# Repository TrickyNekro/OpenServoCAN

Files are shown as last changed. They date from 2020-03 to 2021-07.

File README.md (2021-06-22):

# OpenServoCAN
by El. Provatos

<b>!!! Currently two versions of the Hardware exist, development is going to continue on version 2 !!!</b><br>
<b>!!! Note: There is a design problem ( mechanical fitting ) with the power board, wait for update !!!</b>

An alternative to the boring control boards inside standard size hobby servos!

As it is, the project is far from completion! I have the first boards already, but I do not
have the materials to populate them. I will most probably start a gofundme campaign for these
first stages of the project. So bear with me, this will be an on-going process!

It was a very long time I wanted to make a project like this
Most, for the more expensive ones, hobby servos offer no feed back.
You send them a signal and hope they will reach the targeted position.
This might be good enough for uses in the RC world, but not good enough 
at all for those building robots or anything of a kind that needs feedback.

And thus this project was born! Although I am aware that another OpenServo Project
exists, I wanted to put my own touch into the matter and I tried to do quite a few 
things better, at least compared to the first version (I have not reviewed the second).

- Hardware V1 Capabilities

1) Added CAN-Bus! Yes, that´s a good thing! It might complicate some things especially for beginners
but that´s on what most "unobtainium" servos work in the market. I have not yet decided the 
communications protocol, but I am leaning towards CANopen, suggestions are open!

2) Can support either a potentiometer or an encoder (quadrature or not) for positional control

3) Can operate from 5V - 15V safe zone, but most probably will not have a problem with a 4S LiPo.
Current limiting will be done by software so, if you want to break the DC motor inside or not is
totally up to you!

4) Beefed up MOSFETs with individual MOSFET drivers, just to be able to push that switching 
frequency to the right spot without worrying too much!

- Hardware V2 Capabilities ( added on top of the previous! )

1) Modular! Yes, Modular! There is a Power Board, a CPU / MCU board and a Sensor / Encoder Board.
All are connected on the same bus, through some nice 0,5mm pitch - 30 pin Amphenol connectors. 
That also means of course that everything can change, and the version in connected to the function
specific board and not the whole system. Bored of the microcontroller? Change the MCU board, need
higher voltage? Change the power board? Need more capabilities? If physically allowed, add more
boards! Etc. etc. etc.. 

2) This version uses a magnetic encoder from AMS! Have not tested it yet, but given that it works
well without much interference from the motor, it should be able to give both precision, speed and
universality to the adaptation of the design. And do not forget... bored of the encoder board? Need
something more simple? Design and change it with a potentiometer board! Easy Peasy!!! 

3) One of the main limitation of the previous version was the input voltage. 15V max? How boring! 
This version was aimed to work with 24V and pushing it to 30V should be no problem! Unfortunately
the 100% duty cycle capability is gone as well, but the more efficient all N-Channel MOSFET bridge
should be able to make up the difference! Even if it does not, this was the one big step in being
able to bridge the design to a higher operating voltage, given the much constrained space.

4) There is a digital power meter from Texas Instruments on-board, should offload the processor 
quite a bit! And has also some quite interesting interrupt capabilites that should come in handy.

5) MCU board now has, EEPROM, battery (or better Super-Cap) backed RTC, a temperature sensor and
an RGB LED! How can one live without RGB these days. In all seriousness though, the RTC and EEPROM
should be a good compination for logging data / events and or even be used to wake the device up,
or even be able to develop small scripts for the device to run autonomously. But that´s only a dream
for now, still capability is there!

6) Reverse polarity protection is still here! But I also added some small extras! Some "TVS - like"
suppressors here, some more distributed capacitance there. It should be less noisy and more stable.
Only time will tell as more and more code and testing is being done!

<b> Important 2/11/2020 Update! </b>
I have officially ended the fundraiser for this Project. True to my promise I would like to thank:
Juri Ludwig, Anonymous (from eevblog ;-) ), Vagelis Logaras and Andreas Efthymiadis for their contributions.
Their money have funded a couple mouser orders, the PCBs and some test servos. Which for me is more than
enough that anyone would do for an open project with an open completion date! I can only promise that I
will continue to deliver as much as real life allows me. Thank you! Let your names be immortalized here!

# Donations!

<b>No project on the internet would be great without donations! And Crypto is the future! </b>

In Elon Musk We Trust Dogecoin (DOGE) : DQTDoTPzMencAXoiDVByQjifk2DryYTUPZ <br>
For the old timers Bitcoin (BTC)      : bc1qxqq8dz8md20nyglan9hmk88s894f8h0ywm0fq3 <br>
For the Russian hackers Ethereum(ETH) : 0xAA05e9abD960005df318Ab82aE35A8c47e0096AB <br>

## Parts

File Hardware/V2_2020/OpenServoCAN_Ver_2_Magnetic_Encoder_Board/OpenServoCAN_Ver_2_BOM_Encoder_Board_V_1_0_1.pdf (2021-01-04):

OpenServoCAN_Ver_2_BOM_Encoder_Board_V_1_0_1

Part | Value | Device | Package | Description | Shopping Link | Datasheet
C301 | 100n | GCM155R71H104KE02J | 0402_C | Standard 0402 Capacitor with European Symbol | GCM155R71H104KE02J (https://www.mouser.de/ProductDetail/Murata-Electronics/GCM155R71H104KE02J/?qs=hNud%2FORuBR1wlwGPFWBVDg%3D%3D) | GCM155R71H104KE02J (https://www.mouser.de/datasheet/2/281/murata_03122018_GCM_Series-1310150.pdf)
C302 | 10u | GRM155R60J106ME15D | 0402_C | Standard 0402 Capacitor with European Symbol | GRM155R60J106ME15D (https://www.mouser.de/ProductDetail/Murata-Electronics/GRM155R60J106ME15D/?qs=I53XXhTNm8s65u6%252BR3mHqw%3D%3D) | GRM155R60J106ME15D (https://www.mouser.de/datasheet/2/281/murata_03052018_GRM_Series_1-1310166.pdf)
C303 | 10u | GRM155R60J106ME15D | 0402_C | Standard 0402 Capacitor with European Symbol | GRM155R60J106ME15D (https://www.mouser.de/ProductDetail/Murata-Electronics/GRM155R60J106ME15D/?qs=I53XXhTNm8s65u6%252BR3mHqw%3D%3D) | GRM155R60J106ME15D (https://www.mouser.de/datasheet/2/281/murata_03052018_GRM_Series_1-1310166.pdf)
C304 | 100n | GCM155R71H104KE02J | 0402_C | Standard 0402 Capacitor with European Symbol | GCM155R71H104KE02J (https://www.mouser.de/ProductDetail/Murata-Electronics/GCM155R71H104KE02J/?qs=hNud%2FORuBR1wlwGPFWBVDg%3D%3D) | GCM155R71H104KE02J (https://www.mouser.de/datasheet/2/281/murata_03122018_GCM_Series-1310150.pdf)
C305 | 100n | GCM155R71H104KE02J | 0402_C | Standard 0402 Capacitor with European Symbol | GCM155R71H104KE02J (https://www.mouser.de/ProductDetail/Murata-Electronics/GCM155R71H104KE02J/?qs=hNud%2FORuBR1wlwGPFWBVDg%3D%3D) | GCM155R71H104KE02J (https://www.mouser.de/datasheet/2/281/murata_03122018_GCM_Series-1310150.pdf)
C306 | 100n | GCM155R71H104KE02J | 0402_C | Standard 0402 Capacitor with European Symbol | GCM155R71H104KE02J (https://www.mouser.de/ProductDetail/Murata-Electronics/GCM155R71H104KE02J/?qs=hNud%2FORuBR1wlwGPFWBVDg%3D%3D) | GCM155R71H104KE02J (https://www.mouser.de/datasheet/2/281/murata_03122018_GCM_Series-1310150.pdf)
C307 | 100n | GCM155R71H104KE02J | 0402_C | Standard 0402 Capacitor with European Symbol | GCM155R71H104KE02J (https://www.mouser.de/ProductDetail/Murata-Electronics/GCM155R71H104KE02J/?qs=hNud%2FORuBR1wlwGPFWBVDg%3D%3D) | GCM155R71H104KE02J (https://www.mouser.de/datasheet/2/281/murata_03122018_GCM_Series-1310150.pdf)
C308 | 10u | GRM155R60J106ME15D | 0402_C | Standard 0402 Capacitor with European Symbol | GRM155R60J106ME15D (https://www.mouser.de/ProductDetail/Murata-Electronics/GRM155R60J106ME15D/?qs=I53XXhTNm8s65u6%252BR3mHqw%3D%3D) | GRM155R60J106ME15D (https://www.mouser.de/datasheet/2/281/murata_03052018_GRM_Series_1-1310166.pdf)
C309 | 100n | GCM155R71H104KE02J | 0402_C | Standard 0402 Capacitor with European Symbol | GCM155R71H104KE02J (https://www.mouser.de/ProductDetail/Murata-Electronics/GCM155R71H104KE02J/?qs=hNud%2FORuBR1wlwGPFWBVDg%3D%3D) | GCM155R71H104KE02J (https://www.mouser.de/datasheet/2/281/murata_03122018_GCM_Series-1310150.pdf)
C310 | DMS3R3224R | DMS3R3224R | DMS_3R3_S_CAP | DMS 3R3 0.2 - 0.3 F @ 3V3 6.8X1.8 Coin Super Cap | DMS3R3224R (https://www.reichelt.com/smd-superkondensator-0-22-f-3-3-v-1000-h-ko-dms3r3224r-p244465.html) | DMS3R3224R (https://cdn-reichelt.de/documents/datenblatt/B300/DMS.pdf)
C311 | 100n | GCM155R71H104KE02J | 0402_C | Standard 0402 Capacitor with European Symbol | GCM155R71H104KE02J (https://www.mouser.de/ProductDetail/Murata-Electronics/GCM155R71H104KE02J/?qs=hNud%2FORuBR1wlwGPFWBVDg%3D%3D) | GCM155R71H104KE02J (https://www.mouser.de/datasheet/2/281/murata_03122018_GCM_Series-1310150.pdf)
C312 | 100n | GCM155R71H104KE02J | 0402_C | Standard 0402 Capacitor with European Symbol | GCM155R71H104KE02J (https://www.mouser.de/ProductDetail/Murata-Electronics/GCM155R71H104KE02J/?qs=hNud%2FORuBR1wlwGPFWBVDg%3D%3D) | GCM155R71H104KE02J (https://www.mouser.de/datasheet/2/281/murata_03122018_GCM_Series-1310150.pdf)
IC301 | AS5048A-HTSP-500 | AS5048A-HTSP-500 | TSSOP-14 | 14-bit Angular Position Sensor | AS5048A-HTSP-500 (https://www.mouser.de/ProductDetail/ams/AS5048A-HTSP-500/?qs=YVUHYZFLFLutJ5C0elRlwQ%3D%3D) | AS5048A-HTSP-500 (https://www.mouser.de/datasheet/2/588/AS5048_DS000298_4-00-1100510.pdf)
IC302 | SN74LV1T126DCKRG4 | SN74LV1T126DCKRG4 | SC-70-5 | Single Buffer Gate with 3-State Output | SN74LV1T126DCKRG4 (https://www.mouser.de/ProductDetail/Texas-Instruments/SN74LV1T126DCKRG4/?qs=qSfuJ%252Bfl%2Fd7XMpUR4BtXdA%3D%3D) | SN74LV1T126DCKRG4 (https://www.ti.com/lit/ds/symlink/sn74lv1t126.pdf)
IC303 | SN74LV1T126DCKRG4 | SN74LV1T126DCKRG4 | SC-70-5 | Single Buffer Gate with 3-State Output | SN74LV1T126DCKRG4 (https://www.mouser.de/ProductDetail/Texas-Instruments/SN74LV1T126DCKRG4/?qs=qSfuJ%252Bfl%2Fd7XMpUR4BtXdA%3D%3D) | SN74LV1T126DCKRG4 (https://www.ti.com/lit/ds/symlink/sn74lv1t126.pdf)
IC304 | SN74LV1T126DCKRG4 | SN74LV1T126DCKRG4 | SC-70-5 | Single Buffer Gate with 3-State Output | SN74LV1T126DCKRG4 (https://www.mouser.de/ProductDetail/Texas-Instruments/SN74LV1T126DCKRG4/?qs=qSfuJ%252Bfl%2Fd7XMpUR4BtXdA%3D%3D) | SN74LV1T126DCKRG4 (https://www.ti.com/lit/ds/symlink/sn74lv1t126.pdf)
IC305 | SN74LV1T126DCKRG4 | SN74LV1T126DCKRG4 | SC-70-5 | Single Buffer Gate with 3-State Output | SN74LV1T126DCKRG4 (https://www.mouser.de/ProductDetail/Texas-Instruments/SN74LV1T126DCKRG4/?qs=qSfuJ%252Bfl%2Fd7XMpUR4BtXdA%3D%3D) | SN74LV1T126DCKRG4 (https://www.ti.com/lit/ds/symlink/sn74lv1t126.pdf)
IC306 | TPS79933QDDCRQ1 | TPS79933QDDCRQ1 | SOT-23-5 | LDO 3.3V Voltage Regulators 200mA Output | TPS79933QDDCRQ1 (https://www.mouser.de/ProductDetail/Texas-Instruments/TPS79933QDDCRQ1/?qs=O3wcJz4o8IfzUKU6paImvQ%3D%3D) | TPS79933QDDCRQ1 (https://www.ti.com/lit/ds/symlink/tps799-q1.pdf)
J301 | 10132798-032100LF | 10132798-032100LF | 10132798-032100LF | Amphenol BergStak ® 0.5mm Mezzanine Connector | 10132798-032100LF (https://www.mouser.de/ProductDetail/Amphenol-FCI/10132798-032100LF/) | 10132798-032100LF (https://www.amphenol-icc.com/media/wysiwyg/files/documentation/datasheet/boardwiretoboard/bwb_bergstak_05mm_mezzanine.pdf)
R301 | 100K | ERJ-2RKF1003X | 0402_R | Standard 0402 Resistor with American Symbol | ERJ-2RKF1003X (https://www.mouser.de/ProductDetail/Panasonic/ERJ-2RKF1003X/?qs=sGAEpiMZZMtlubZbdhIBIHcx2Q2RnT7K1YMPDp9rJM8%3D) | ERJ-2RKF1003X (https://www.mouser.de/datasheet/2/315/AOA0000C304-1149620.pdf)
R302 | 100K | ERJ-2RKF1003X | 0402_R | Standard 0402 Resistor with American Symbol | ERJ-2RKF1003X (https://www.mouser.de/ProductDetail/Panasonic/ERJ-2RKF1003X/?qs=sGAEpiMZZMtlubZbdhIBIHcx2Q2RnT7K1YMPDp9rJM8%3D) | ERJ-2RKF1003X (https://www.mouser.de/datasheet/2/315/AOA0000C304-1149620.pdf)
R303 | 100K | ERJ-2RKF1003X | 0402_R | Standard 0402 Resistor with American Symbol | ERJ-2RKF1003X (https://www.mouser.de/ProductDetail/Panasonic/ERJ-2RKF1003X/?qs=sGAEpiMZZMtlubZbdhIBIHcx2Q2RnT7K1YMPDp9rJM8%3D) | ERJ-2RKF1003X (https://www.mouser.de/datasheet/2/315/AOA0000C304-1149620.pdf)
R304 | 100K | ERJ-2RKF1003X | 0402_R | Standard 0402 Resistor with American Symbol | ERJ-2RKF1003X (https://www.mouser.de/ProductDetail/Panasonic/ERJ-2RKF1003X/?qs=sGAEpiMZZMtlubZbdhIBIHcx2Q2RnT7K1YMPDp9rJM8%3D) | ERJ-2RKF1003X (https://www.mouser.de/datasheet/2/315/AOA0000C304-1149620.pdf)
R305 | 100K | ERJ-2RKF1003X | 0402_R | Standard 0402 Resistor with American Symbol | ERJ-2RKF1003X (https://www.mouser.de/ProductDetail/Panasonic/ERJ-2RKF1003X/?qs=sGAEpiMZZMtlubZbdhIBIHcx2Q2RnT7K1YMPDp9rJM8%3D) | ERJ-2RKF1003X (https://www.mouser.de/datasheet/2/315/AOA0000C304-1149620.pdf)
R306 | 100K | ERJ-2RKF1003X | 0402_R | Standard 0402 Resistor with American Symbol | ERJ-2RKF1003X (https://www.mouser.de/ProductDetail/Panasonic/ERJ-2RKF1003X/?qs=sGAEpiMZZMtlubZbdhIBIHcx2Q2RnT7K1YMPDp9rJM8%3D) | ERJ-2RKF1003X (https://www.mouser.de/datasheet/2/315/AOA0000C304-1149620.pdf)
R307 | 100K | ERJ-2RKF1003X | 0402_R | Standard 0402 Resistor with American Symbol | ERJ-2RKF1003X (https://www.mouser.de/ProductDetail/Panasonic/ERJ-2RKF1003X/?qs=sGAEpiMZZMtlubZbdhIBIHcx2Q2RnT7K1YMPDp9rJM8%3D) | ERJ-2RKF1003X (https://www.mouser.de/datasheet/2/315/AOA0000C304-1149620.pdf)
R308 | 100K | ERJ-2RKF1003X | 0402_R | Standard 0402 Resistor with American Symbol | ERJ-2RKF1003X (https://www.mouser.de/ProductDetail/Panasonic/ERJ-2RKF1003X/?qs=sGAEpiMZZMtlubZbdhIBIHcx2Q2RnT7K1YMPDp9rJM8%3D) | ERJ-2RKF1003X (https://www.mouser.de/datasheet/2/315/AOA0000C304-1149620.pdf)
R309 | 47 | ERJ-2RKF47R0X | 0402_R | Standard 0402 Resistor with American Symbol | ERJ-2RKF47R0X (https://www.mouser.de/ProductDetail/Panasonic/ERJ-2RKF47R0X/) | ERJ-2RKF47R0X (https://www.mouser.de/datasheet/2/315/AOA0000C304-1149620.pdf)
R310 | 47 | ERJ-2RKF47R0X | 0402_R | Standard 0402 Resistor with American Symbol | ERJ-2RKF47R0X (https://www.mouser.de/ProductDetail/Panasonic/ERJ-2RKF47R0X/) | ERJ-2RKF47R0X (https://www.mouser.de/datasheet/2/315/AOA0000C304-1149620.pdf)
R311 | 47 | ERJ-2RKF47R0X | 0402_R | Standard 0402 Resistor with American Symbol | ERJ-2RKF47R0X (https://www.mouser.de/ProductDetail/Panasonic/ERJ-2RKF47R0X/) | ERJ-2RKF47R0X (https://www.mouser.de/datasheet/2/315/AOA0000C304-1149620.pdf)
R312 | 47 | ERJ-2RKF47R0X | 0402_R | Standard 0402 Resistor with American Symbol | ERJ-2RKF47R0X (https://www.mouser.de/ProductDetail/Panasonic/ERJ-2RKF47R0X/) | ERJ-2RKF47R0X (https://www.mouser.de/datasheet/2/315/AOA0000C304-1149620.pdf)
R313 | 1k | ERJ-2RKF1001X | 0402_R | Standard 0402 Resistor with American Symbol | ERJ-2RKF1001X (https://www.mouser.de/ProductDetail/Panasonic/ERJ-2RKF1001X/) | ERJ-2RKF1001X (https://www.mouser.de/datasheet/2/315/AOA0000C304-1149620.pdf)
R314 | 1k | ERJ-2RKF1001X | 0402_R | Standard 0402 Resistor with American Symbol | ERJ-2RKF1001X (https://www.mouser.de/ProductDetail/Panasonic/ERJ-2RKF1001X/) | ERJ-2RKF1001X (https://www.mouser.de/datasheet/2/315/AOA0000C304-1149620.pdf)
R315 | 470 | ERJ-2RKF4700X | 0402_R | Standard 0402 Resistor with American Symbol | ERJ-2RKF4700X (https://www.mouser.de/ProductDetail/Panasonic/ERJ-2RKF4700X/) | ERJ-2RKF4700X (https://www.mouser.de/datasheet/2/315/AOA0000C304-1149620.pdf)
R316 | 10 | ERJ-2RKF10R0X | 0402_R | Standard 0402 Resistor with American Symbol | ERJ-2RKF10R0X (https://www.mouser.de/ProductDetail/Panasonic/ERJ-2RKF10R0X/) | ERJ-2RKF10R0X (https://www.mouser.de/datasheet/2/315/AOA0000C304-1149620.pdf)
R317 | 10 | ERJ-2RKF10R0X | 0402_R | Standard 0402 Resistor with American Symbol | ERJ-2RKF10R0X (https://www.mouser.de/ProductDetail/Panasonic/ERJ-2RKF10R0X/) | ERJ-2RKF10R0X (https://www.mouser.de/datasheet/2/315/AOA0000C304-1149620.pdf)
R318 | 1k | ERJ-2RKF1001X | 0402_R | Standard 0402 Resistor with American Symbol | ERJ-2RKF1001X (https://www.mouser.de/ProductDetail/Panasonic/ERJ-2RKF1001X/) | ERJ-2RKF1001X (https://www.mouser.de/datasheet/2/315/AOA0000C304-1149620.pdf)
T301 | UMX1NFHATN | UMX1NFHATN | SC-70-6 | Bipolar Transistor Pair ( NPN + NPN ) | UMX1NFHATN (https://www.mouser.de/ProductDetail/ROHM-Semiconductor/UMX1NFHATN/) | UMX1NFHATN (https://www.mouser.de/datasheet/2/348/umx1nfha-e-1872402.pdf)

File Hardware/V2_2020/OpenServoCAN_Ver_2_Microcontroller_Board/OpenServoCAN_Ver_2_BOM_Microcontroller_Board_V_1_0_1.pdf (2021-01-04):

OpenServoCAN_Ver_2_Microcontroller_Board_V_1_0_1

Part | Value | Device | Package | Description | Shopping Link | Datasheet
C201 | 100n | GCM155R71H104KE02J | 0402_C | Standard 0402 Capacitor with European Symbol | GCM155R71H104KE02J (https://www.mouser.de/ProductDetail/Murata-Electronics/GCM155R71H104KE02J/?qs=hNud%2FORuBR1wlwGPFWBVDg%3D%3D) | GCM155R71H104KE02J (https://www.mouser.de/datasheet/2/281/murata_03122018_GCM_Series-1310150.pdf)
C202 | 2u2 | LMK105BJ225KV-F | 0402_C | Standard 0402 Capacitor with European Symbol | LMK105BJ225KV-F (https://www.mouser.de/ProductDetail/Taiyo-Yuden/LMK105BJ225KV-F/) | LMK105BJ225KV-F (https://www.mouser.de/datasheet/2/396/mlcc02_e-1307760.pdf)
C203 | 100n | GCM155R71H104KE02J | 0402_C | Standard 0402 Capacitor with European Symbol | GCM155R71H104KE02J (https://www.mouser.de/ProductDetail/Murata-Electronics/GCM155R71H104KE02J/?qs=hNud%2FORuBR1wlwGPFWBVDg%3D%3D) | GCM155R71H104KE02J (https://www.mouser.de/datasheet/2/281/murata_03122018_GCM_Series-1310150.pdf)
C204 | 100n | GCM155R71H104KE02J | 0402_C | Standard 0402 Capacitor with European Symbol | GCM155R71H104KE02J (https://www.mouser.de/ProductDetail/Murata-Electronics/GCM155R71H104KE02J/?qs=hNud%2FORuBR1wlwGPFWBVDg%3D%3D) | GCM155R71H104KE02J (https://www.mouser.de/datasheet/2/281/murata_03122018_GCM_Series-1310150.pdf)
C205 | 100n | GCM155R71H104KE02J | 0402_C | Standard 0402 Capacitor with European Symbol | GCM155R71H104KE02J (https://www.mouser.de/ProductDetail/Murata-Electronics/GCM155R71H104KE02J/?qs=hNud%2FORuBR1wlwGPFWBVDg%3D%3D) | GCM155R71H104KE02J (https://www.mouser.de/datasheet/2/281/murata_03122018_GCM_Series-1310150.pdf)
C206 | 22p | 04025A220JAT4A | 0402_C | Standard 0402 Capacitor with European Symbol | 04025A220JAT4A (https://www.mouser.de/ProductDetail/AVX/04025A220JAT4A/?qs=i7%252BfZ0iplmWikHQFZS%252BeyA%3D%3D) | 04025A220JAT4A (https://www.mouser.de/datasheet/2/40/C0GNP0_Dielectric-951274.pdf)
C207 | 22p | 04025A220JAT4A | 0402_C | Standard 0402 Capacitor with European Symbol | 04025A220JAT4A (https://www.mouser.de/ProductDetail/AVX/04025A220JAT4A/?qs=i7%252BfZ0iplmWikHQFZS%252BeyA%3D%3D) | 04025A220JAT4A (https://www.mouser.de/datasheet/2/40/C0GNP0_Dielectric-951274.pdf)
C208 | 100n | GCM155R71H104KE02J | 0402_C | Standard 0402 Capacitor with European Symbol | GCM155R71H104KE02J (https://www.mouser.de/ProductDetail/Murata-Electronics/GCM155R71H104KE02J/?qs=hNud%2FORuBR1wlwGPFWBVDg%3D%3D) | GCM155R71H104KE02J (https://www.mouser.de/datasheet/2/281/murata_03122018_GCM_Series-1310150.pdf)
C209 | 100n | GCM155R71H104KE02J | 0402_C | Standard 0402 Capacitor with European Symbol | GCM155R71H104KE02J (https://www.mouser.de/ProductDetail/Murata-Electronics/GCM155R71H104KE02J/?qs=hNud%2FORuBR1wlwGPFWBVDg%3D%3D) | GCM155R71H104KE02J (https://www.mouser.de/datasheet/2/281/murata_03122018_GCM_Series-1310150.pdf)
C210 | 100n | GCM155R71H104KE02J | 0402_C | Standard 0402 Capacitor with European Symbol | GCM155R71H104KE02J (https://www.mouser.de/ProductDetail/Murata-Electronics/GCM155R71H104KE02J/?qs=hNud%2FORuBR1wlwGPFWBVDg%3D%3D) | GCM155R71H104KE02J (https://www.mouser.de/datasheet/2/281/murata_03122018_GCM_Series-1310150.pdf)
IC201 | PIC18F26K83-I/ML | PIC18F26K83-I/ML | QFN-28 | PIC18(L)F25/26K83 | PIC18F26K83-I/ML (https://www.mouser.de/ProductDetail/Microchip-Technology/PIC18F26K83-I-ML/) | PIC18F26K83-I/ML (https://www.mouser.de/datasheet/2/268/40001943A-1222654.pdf)
IC202 | MCP9808T-E/MC | MCP9808T-E/MC | DFN_2X3_MICROCHIP | MCP9808 | MCP9808T-E/MC (https://www.mouser.de/ProductDetail/Microchip-Technology/MCP9808T-E-MC/) | MCP9808T-E/MC (https://www.mouser.de/datasheet/2/268/25095A-15487.pdf)
IC203 | MCP7940NT-I/MNY | MCP7940NT-I/MNY | DFN_2X3_MICROCHIP | MCP7940N | MCP7940NT-I/MNY (https://www.mouser.de/ProductDetail/Microchip-Technology/MCP7940NT-I-MNY/) | MCP7940NT-I/MNY (https://www.mouser.de/datasheet/2/268/25010A-71550.pdf)
IC204 | 24LC64T-E/MNY | 24LC64T-E/MNY | DFN_2X3_MICROCHIP | 24LCxx Type EEPROM | 24LC64T-E/MNY (https://www.mouser.de/ProductDetail/Microchip-Technology/24LC64T-E-MNY/) | 24LC64T-E/MNY (https://www.mouser.de/datasheet/2/268/21189T-264996.pdf)
J201 | 53047-0510 | PIC-ICSP-MICRO | PICOBLADE-5 | Microchip PIC ICSP based on a 5 PIN Molex PICO-Blade | 53047-0510 (https://www.mouser.de/ProductDetail/Molex/53047-0510/) | 53047-0510 (https://www.mouser.de/datasheet/2/276/0530470510_PCB_HEADERS-171009.pdf)
J202 | 10132798-032100LF | 10132798-032100LF | 10132798-032100LF | Amphenol BergStak ® 0.5mm Mezzanine Connector | 10132798-032100LF (https://www.mouser.de/ProductDetail/Amphenol-FCI/10132798-032100LF/) | 10132798-032100LF (https://www.amphenol-icc.com/media/wysiwyg/files/documentation/datasheet/boardwiretoboard/bwb_bergstak_05mm_mezzanine.pdf)
J203 | 10132797-035100LF | 10132797-035100LF | 10132797-035100LF | Amphenol BergStak ® 0.5mm Mezzanine Connector | 10132797-035100LF (https://www.mouser.de/ProductDetail/Amphenol-FCI/10132797-035100LF/) | 10132797-035100LF (https://www.amphenol-icc.com/media/wysiwyg/files/documentation/datasheet/boardwiretoboard/bwb_bergstak_05mm_mezzanine.pdf)
LED201 | IN-S126TASRGB | IN-S126TASRGB | 1206_RGB_LED | Side View RGB LED from Lite-On | IN-S126TASRGB (https://www.mouser.de/ProductDetail/Inolux/IN-S126TASRGB/) | IN-S126TASRGB (https://www.mouser.de/datasheet/2/180/IN_S126TASRGB_V1_1-1488266.pdf)
Q201 | LFXTAL009678 | LFXTAL009678 | LFXTAL009678 | LFXTAL009678 | LFXTAL009678 (https://www.mouser.de/Search/Refine?Keyword=LFXTAL009678) | LFXTAL009678 (https://www.mouser.de/datasheet/2/741/LFXTAL009678Cutt-952301.pdf)
R201 | 4k7 | ERJ-2RKF4701X | 0402_R | Standard 0402 Resistor with American Symbol | ERJ-2RKF4701X (https://www.mouser.de/ProductDetail/Panasonic/ERJ-2RKF4701X/) | ERJ-2RKF4701X (https://www.mouser.de/datasheet/2/315/AOA0000C304-1149620.pdf)
R202 | 470 | ERJ-2RKF4700X | 0402_R | Standard 0402 Resistor with American Symbol | ERJ-2RKF4700X (https://www.mouser.de/ProductDetail/Panasonic/ERJ-2RKF4700X/) | ERJ-2RKF4700X (https://www.mouser.de/datasheet/2/315/AOA0000C304-1149620.pdf)
R203 | 220 | ERJ-2RKF2200X | 0402_R | Standard 0402 Resistor with American Symbol | ERJ-2RKF2200X (https://www.mouser.de/ProductDetail/Panasonic/ERJ-2RKF2200X/) | ERJ-2RKF2200X (https://www.mouser.de/datasheet/2/315/AOA0000C304-1149620.pdf)
R204 | 220 | ERJ-2RKF2200X | 0402_R | Standard 0402 Resistor with American Symbol | ERJ-2RKF2200X (https://www.mouser.de/ProductDetail/Panasonic/ERJ-2RKF2200X/) | ERJ-2RKF2200X (https://www.mouser.de/datasheet/2/315/AOA0000C304-1149620.pdf)
R205 | 220 | ERJ-2RKF2200X | 0402_R | Standard 0402 Resistor with American Symbol | ERJ-2RKF2200X (https://www.mouser.de/ProductDetail/Panasonic/ERJ-2RKF2200X/) | ERJ-2RKF2200X (https://www.mouser.de/datasheet/2/315/AOA0000C304-1149620.pdf)
R206 | 4k7 | ERJ-2RKF4701X | 0402_R | Standard 0402 Resistor with American Symbol | ERJ-2RKF4701X (https://www.mouser.de/ProductDetail/Panasonic/ERJ-2RKF4701X/) | ERJ-2RKF4701X (https://www.mouser.de/datasheet/2/315/AOA0000C304-1149620.pdf)
R207 | 4k7 | ERJ-2RKF4701X | 0402_R | Standard 0402 Resistor with American Symbol | ERJ-2RKF4701X (https://www.mouser.de/ProductDetail/Panasonic/ERJ-2RKF4701X/) | ERJ-2RKF4701X (https://www.mouser.de/datasheet/2/315/AOA0000C304-1149620.pdf)
R208 | 4k7 | ERJ-2RKF4701X | 0402_R | Standard 0402 Resistor with American Symbol | ERJ-2RKF4701X (https://www.mouser.de/ProductDetail/Panasonic/ERJ-2RKF4701X/) | ERJ-2RKF4701X (https://www.mouser.de/datasheet/2/315/AOA0000C304-1149620.pdf)
R209 | 4k7 | ERJ-2RKF4701X | 0402_R | Standard 0402 Resistor with American Symbol | ERJ-2RKF4701X (https://www.mouser.de/ProductDetail/Panasonic/ERJ-2RKF4701X/) | ERJ-2RKF4701X (https://www.mouser.de/datasheet/2/315/AOA0000C304-1149620.pdf)
R210 | 470 | ERJ-2RKF4700X | 0402_R | Standard 0402 Resistor with American Symbol | ERJ-2RKF4700X (https://www.mouser.de/ProductDetail/Panasonic/ERJ-2RKF4700X/) | ERJ-2RKF4700X (https://www.mouser.de/datasheet/2/315/AOA0000C304-1149620.pdf)
R211 | 470 | ERJ-2RKF4700X | 0402_R | Standard 0402 Resistor with American Symbol | ERJ-2RKF4700X (https://www.mouser.de/ProductDetail/Panasonic/ERJ-2RKF4700X/) | ERJ-2RKF4700X (https://www.mouser.de/datasheet/2/315/AOA0000C304-1149620.pdf)
R212 | 47 | ERJ-2RKF47R0X | 0402_R | Standard 0402 Resistor with American Symbol | ERJ-2RKF47R0X (https://www.mouser.de/ProductDetail/Panasonic/ERJ-2RKF47R0X/) | ERJ-2RKF47R0X (https://www.mouser.de/datasheet/2/315/AOA0000C304-1149620.pdf)
R213 | 47 | ERJ-2RKF47R0X | 0402_R | Standard 0402 Resistor with American Symbol | ERJ-2RKF47R0X (https://www.mouser.de/ProductDetail/Panasonic/ERJ-2RKF47R0X/) | ERJ-2RKF47R0X (https://www.mouser.de/datasheet/2/315/AOA0000C304-1149620.pdf)
R214 | 47 | ERJ-2RKF47R0X | 0402_R | Standard 0402 Resistor with American Symbol | ERJ-2RKF47R0X (https://www.mouser.de/ProductDetail/Panasonic/ERJ-2RKF47R0X/) | ERJ-2RKF47R0X (https://www.mouser.de/datasheet/2/315/AOA0000C304-1149620.pdf)

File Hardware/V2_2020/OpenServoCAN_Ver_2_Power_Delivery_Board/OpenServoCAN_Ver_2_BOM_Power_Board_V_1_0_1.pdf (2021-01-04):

OpenServoCAN_Ver_2_BOM_Power_Board_V_1_0_1

Part | Value | Device | Package | Description | Shopping Link | Datasheet
C101 | 220n | CL10A224KB8NNNC | 0603_C | Standard 0603 Capacitor with European Symbol | CL10A224KB8NNNC (https://www.mouser.de/ProductDetail/Samsung-Electro-Mechanics/CL10A224KB8NNNC/?qs=uwxL4vQweFONfCk4qeShcQ%3D%3D) | CL10A224KB8NNNC (https://www.mouser.de/datasheet/2/585/MLCC-1837944.pdf)
C102 | 220n | CL10A224KB8NNNC | 0603_C | Standard 0603 Capacitor with European Symbol | CL10A224KB8NNNC (https://www.mouser.de/ProductDetail/Samsung-Electro-Mechanics/CL10A224KB8NNNC/?qs=uwxL4vQweFONfCk4qeShcQ%3D%3D) | CL10A224KB8NNNC (https://www.mouser.de/datasheet/2/585/MLCC-1837944.pdf)
C103 | 10u | GRM155R60J106ME15D | 0402_C | Standard 0402 Capacitor with European Symbol | GRM155R60J106ME15D (https://www.mouser.de/ProductDetail/Murata-Electronics/GRM155R60J106ME15D/?qs=I53XXhTNm8s65u6%252BR3mHqw%3D%3D) | GRM155R60J106ME15D (https://www.mouser.de/datasheet/2/281/murata_03052018_GRM_Series_1-1310166.pdf)
C104 | 10u | GRM155R60J106ME15D | 0402_C | Standard 0402 Capacitor with European Symbol | GRM155R60J106ME15D (https://www.mouser.de/ProductDetail/Murata-Electronics/GRM155R60J106ME15D/?qs=I53XXhTNm8s65u6%252BR3mHqw%3D%3D) | GRM155R60J106ME15D (https://www.mouser.de/datasheet/2/281/murata_03052018_GRM_Series_1-1310166.pdf)
C105 | 100n | GCM155R71H104KE02J | 0402_C | Standard 0402 Capacitor with European Symbol | GCM155R71H104KE02J (https://www.mouser.de/ProductDetail/Murata-Electronics/GCM155R71H104KE02J/?qs=hNud%2FORuBR1wlwGPFWBVDg%3D%3D) | GCM155R71H104KE02J (https://www.mouser.de/datasheet/2/281/murata_03122018_GCM_Series-1310150.pdf)
C106 | 100n | GCM155R71H104KE02J | 0402_C | Standard 0402 Capacitor with European Symbol | GCM155R71H104KE02J (https://www.mouser.de/ProductDetail/Murata-Electronics/GCM155R71H104KE02J/?qs=hNud%2FORuBR1wlwGPFWBVDg%3D%3D) | GCM155R71H104KE02J (https://www.mouser.de/datasheet/2/281/murata_03122018_GCM_Series-1310150.pdf)
C107 | 100n | GCM155R71H104KE02J | 0402_C | Standard 0402 Capacitor with European Symbol | GCM155R71H104KE02J (https://www.mouser.de/ProductDetail/Murata-Electronics/GCM155R71H104KE02J/?qs=hNud%2FORuBR1wlwGPFWBVDg%3D%3D) | GCM155R71H104KE02J (https://www.mouser.de/datasheet/2/281/murata_03122018_GCM_Series-1310150.pdf)
C108 | 10u | GRM155R60J106ME15D | 0402_C | Standard 0402 Capacitor with European Symbol | GRM155R60J106ME15D (https://www.mouser.de/ProductDetail/Murata-Electronics/GRM155R60J106ME15D/?qs=I53XXhTNm8s65u6%252BR3mHqw%3D%3D) | GRM155R60J106ME15D (https://www.mouser.de/datasheet/2/281/murata_03052018_GRM_Series_1-1310166.pdf)
C109 | 10u | GRM155R60J106ME15D | 0402_C | Standard 0402 Capacitor with European Symbol | GRM155R60J106ME15D (https://www.mouser.de/ProductDetail/Murata-Electronics/GRM155R60J106ME15D/?qs=I53XXhTNm8s65u6%252BR3mHqw%3D%3D) | GRM155R60J106ME15D (https://www.mouser.de/datasheet/2/281/murata_03052018_GRM_Series_1-1310166.pdf)
C110 | 1u | CL10A105KB8NNNC | 0603_C | Standard 0603 Capacitor with European Symbol | CL10A105KB8NNNC (https://www.mouser.de/ProductDetail/Samsung-Electro-Mechanics/CL10A105KB8NNNC/?qs=ktYoCbbtCSJz4pFCLWXd5g%3D%3D) | CL10A105KB8NNNC (https://www.mouser.de/datasheet/2/585/MLCC-1837944.pdf)
C111 | 1u | CL10A105KB8NNNC | 0603_C | Standard 0603 Capacitor with European Symbol | CL10A105KB8NNNC (https://www.mouser.de/ProductDetail/Samsung-Electro-Mechanics/CL10A105KB8NNNC/?qs=ktYoCbbtCSJz4pFCLWXd5g%3D%3D) | CL10A105KB8NNNC (https://www.mouser.de/datasheet/2/585/MLCC-1837944.pdf)
C112 | 1u | CL10A105KB8NNNC | 0603_C | Standard 0603 Capacitor with European Symbol | CL10A105KB8NNNC (https://www.mouser.de/ProductDetail/Samsung-Electro-Mechanics/CL10A105KB8NNNC/?qs=ktYoCbbtCSJz4pFCLWXd5g%3D%3D) | CL10A105KB8NNNC (https://www.mouser.de/datasheet/2/585/MLCC-1837944.pdf)
C113 | 1u | CL10A105KB8NNNC | 0603_C | Standard 0603 Capacitor with European Symbol | CL10A105KB8NNNC (https://www.mouser.de/ProductDetail/Samsung-Electro-Mechanics/CL10A105KB8NNNC/?qs=ktYoCbbtCSJz4pFCLWXd5g%3D%3D) | CL10A105KB8NNNC (https://www.mouser.de/datasheet/2/585/MLCC-1837944.pdf)
C114 | 1u | CL10A105KB8NNNC | 0603_C | Standard 0603 Capacitor with European Symbol | CL10A105KB8NNNC (https://www.mouser.de/ProductDetail/Samsung-Electro-Mechanics/CL10A105KB8NNNC/?qs=ktYoCbbtCSJz4pFCLWXd5g%3D%3D) | CL10A105KB8NNNC (https://www.mouser.de/datasheet/2/585/MLCC-1837944.pdf)
C115 | 1u | CL10A105KB8NNNC | 0603_C | Standard 0603 Capacitor with European Symbol | CL10A105KB8NNNC (https://www.mouser.de/ProductDetail/Samsung-Electro-Mechanics/CL10A105KB8NNNC/?qs=ktYoCbbtCSJz4pFCLWXd5g%3D%3D) | CL10A105KB8NNNC (https://www.mouser.de/datasheet/2/585/MLCC-1837944.pdf)
C116 | 1u | CL10A105KB8NNNC | 0603_C | Standard 0603 Capacitor with European Symbol | CL10A105KB8NNNC (https://www.mouser.de/ProductDetail/Samsung-Electro-Mechanics/CL10A105KB8NNNC/?qs=ktYoCbbtCSJz4pFCLWXd5g%3D%3D) | CL10A105KB8NNNC (https://www.mouser.de/datasheet/2/585/MLCC-1837944.pdf)
C117 | 10n | GCM155R71H103KA55D | 0402_C | Standard 0402 Capacitor with European Symbol | GCM155R71H103KA55D (https://www.mouser.de/ProductDetail/Murata-Electronics/GCM155R71H103KA55D/?qs=aEuGZpxfbxUFaK62TPaKIA%3D%3D) | GCM155R71H103KA55D (https://www.mouser.de/datasheet/2/281/murata_03122018_GCM_Series-1310150.pdf)
C118 | 470p | CC1206JRNPO0BN471 | 1206_C | Standard 1206 Capacitor with European Symbol | CC1206JRNPO0BN471 (https://www.mouser.de/ProductDetail/Yageo/CC1206JRNPO0BN471/?qs=AgBp2OyFlx8rV3mvW5uGXA%3D%3D) | CC1206JRNPO0BN471 (https://www.mouser.de/datasheet/2/447/UPY_NP0X7R_MV_100_to_630V_21-1947934.pdf)
C119 | 47p | CC1206JRNPO0BN470 | 1206_C | Standard 1206 Capacitor with European Symbol | CC1206JRNPO0BN470 (https://www.mouser.de/ProductDetail/Yageo/CC1206JRNPO0BN470/) | CC1206JRNPO0BN470 (https://www.mouser.de/datasheet/2/447/UPY_NP0X7R_MV_100_to_630V_21-1947934.pdf)
C120 | 47p | CC1206JRNPO0BN470 | 1206_C | Standard 1206 Capacitor with European Symbol | CC1206JRNPO0BN470 (https://www.mouser.de/ProductDetail/Yageo/CC1206JRNPO0BN470/) | CC1206JRNPO0BN470 (https://www.mouser.de/datasheet/2/447/UPY_NP0X7R_MV_100_to_630V_21-1947934.pdf)
D101 | DDZ12CSF-7 | DDZ12CSF-7 | SOD-323 | Zener Diodes 500mW 12.05V Zener 0.07uA 11.20 | DDZ12CSF-7 (https://www.mouser.de/ProductDetail/Diodes-Incorporated/DDZ12CSF-7/) | DDZ12CSF-7 (https://www.mouser.de/datasheet/2/115/ds31987-65362.pdf)
D102 | PMEG4010ESBYL | PMEG4010ESBYL | DSN1006-2 | 40 V, 1 A low VF MEGA Schottky | PMEG4010ESBYL (https://www.mouser.de/ProductDetail/Nexperia/PMEG4010ESBYL/?qs=bel5lzaZNxTQEUPrzEQoCw%3D%3D) | PMEG4010ESBYL (https://www.mouser.de/datasheet/2/916/PMEG4010ESB-1320302.pdf)
D103 | TVS2701DRBR | TVS2701DRBR | VSON-8-DRB0008A | TVSxx01 Series of Texas Instruments Fast-Clamp TVS | TVS2701DRBR (https://www.mouser.de/ProductDetail/Texas-Instruments/TVS2701DRBR/) | TVS2701DRBR (https://www.ti.com/lit/ds/symlink/tvs2701.pdf)
D104 | TVS2700DRVR | TVS2700DRVR | WSON-6 | TVSxx00 Series of Texas Instruments Fast-Clamp TVS | TVS2700DRVR (https://www.mouser.de/ProductDetail/Texas-Instruments/TVS2700DRVR/) | TVS2700DRVR (https://www.ti.com/lit/ds/symlink/tvs2700.pdf)
IC101 | MCP14700-E/MF | MCP14700-E/MF | DFN_8_3X3X09_MF | Dual Input Synchronous MOSFET Driver | MCP14700-E/MF (https://www.mouser.de/ProductDetail/Microchip-Technology/MCP14700-E-MF/?qs=X8nz4ozed5gysS6OQjCf4w%3D%3D) | MCP14700-E/MF (https://www.mouser.de/datasheet/2/268/22201a-53003.pdf)
IC102 | MCP14700-E/MF | MCP14700-E/MF | DFN_8_3X3X09_MF | Dual Input Synchronous MOSFET Driver | MCP14700-E/MF (https://www.mouser.de/ProductDetail/Microchip-Technology/MCP14700-E-MF/?qs=X8nz4ozed5gysS6OQjCf4w%3D%3D) | MCP14700-E/MF (https://www.mouser.de/datasheet/2/268/22201a-53003.pdf)
IC103 | LDO40LPURY | LDO40LPURY | DFN6-3X3 | 400 mA, 38 V low-dropout regulator | LDO40LPURY (https://www.mouser.de/ProductDetail/STMicroelectronics/LDO40LPURY/?qs=qSfuJ%252Bfl%2Fd6C3Fwu6g7H1A%3D%3D) | LDO40LPURY (https://www.mouser.de/datasheet/2/389/ldo40l-1843445.pdf)
IC104 | INA226AIDGSR | INA226AIDGSR | VSSOP-10 | Bi-DirectionalCurrentand PowerMonitor with I²C | INA226AIDGSR (https://www.mouser.de/ProductDetail/Texas-Instruments/INA226AIDGSR/?qs=tQG3bEuiOZD4quG3egR36g%3D%3D) | INA226AIDGSR (https://www.ti.com/lit/ds/symlink/ina226.pdf)
IC105 | ATA6560-GBQW-N | ATA6560-GBQW-N | VDFN-8-EP | High-Speed CAN Transceiver – CAN FD Ready | ATA6560-GBQW-N (https://www.mouser.de/ProductDetail/Microchip-Technology-Atmel/ATA6560-GBQW-N/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) | ATA6560-GBQW-N (https://www.mouser.de/datasheet/2/268/ATA6560_ATA6561_High_Speed_CAN_Transceiver_DS20005-1384933.pdf)
J101 | 10132797-035100LF | 10132797-035100LF | 10132797-035100LF | Amphenol BergStak ® 0.5mm Mezzanine Connector | 10132797-035100LF (https://www.mouser.de/ProductDetail/Amphenol-FCI/10132797-035100LF/) | 10132797-035100LF (https://www.amphenol-icc.com/media/wysiwyg/files/documentation/datasheet/boardwiretoboard/bwb_bergstak_05mm_mezzanine.pdf)
J102 | 504255 | 504255 | 504255 | Header 4 Pin Male Black SMT Right-Angle by ERNI | 504255 (https://www.mouser.de/ProductDetail/ERNI/504255/?qs=Cb2nCFKsA8quq588izW8Fw%3D%3D) | 504255 (https://www.mouser.de/datasheet/2/625/ERNI_Electronics_01132020_504254-1708722.pdf)
R101 | 10 | ERJ-2RKF10R0X | 0402_R | Standard 0402 Resistor with American Symbol | ERJ-2RKF10R0X (https://www.mouser.de/ProductDetail/Panasonic/ERJ-2RKF10R0X/) | ERJ-2RKF10R0X (https://www.mouser.de/datasheet/2/315/AOA0000C304-1149620.pdf)
R102 | 10 | ERJ-2RKF10R0X | 0402_R | Standard 0402 Resistor with American Symbol | ERJ-2RKF10R0X (https://www.mouser.de/ProductDetail/Panasonic/ERJ-2RKF10R0X/) | ERJ-2RKF10R0X (https://www.mouser.de/datasheet/2/315/AOA0000C304-1149620.pdf)
R103 | 10 | ERJ-2RKF10R0X | 0402_R | Standard 0402 Resistor with American Symbol | ERJ-2RKF10R0X (https://www.mouser.de/ProductDetail/Panasonic/ERJ-2RKF10R0X/) | ERJ-2RKF10R0X (https://www.mouser.de/datasheet/2/315/AOA0000C304-1149620.pdf)
R104 | 10 | ERJ-2RKF10R0X | 0402_R | Standard 0402 Resistor with American Symbol | ERJ-2RKF10R0X (https://www.mouser.de/ProductDetail/Panasonic/ERJ-2RKF10R0X/) | ERJ-2RKF10R0X (https://www.mouser.de/datasheet/2/315/AOA0000C304-1149620.pdf)
R105 | 1K | ERJ-2RKF1001X | 0402_R | Standard 0402 Resistor with American Symbol | ERJ-2RKF1001X (https://www.mouser.de/ProductDetail/Panasonic/ERJ-2RKF1001X/) | ERJ-2RKF1001X (https://www.mouser.de/datasheet/2/315/AOA0000C304-1149620.pdf)
R106 | 1K | ERJ-2RKF1001X | 0402_R | Standard 0402 Resistor with American Symbol | ERJ-2RKF1001X (https://www.mouser.de/ProductDetail/Panasonic/ERJ-2RKF1001X/) | ERJ-2RKF1001X (https://www.mouser.de/datasheet/2/315/AOA0000C304-1149620.pdf)
R107 | 1K | ERJ-2RKF1001X | 0402_R | Standard 0402 Resistor with American Symbol | ERJ-2RKF1001X (https://www.mouser.de/ProductDetail/Panasonic/ERJ-2RKF1001X/) | ERJ-2RKF1001X (https://www.mouser.de/datasheet/2/315/AOA0000C304-1149620.pdf)
R108 | 1K | ERJ-2RKF1001X | 0402_R | Standard 0402 Resistor with American Symbol | ERJ-2RKF1001X (https://www.mouser.de/ProductDetail/Panasonic/ERJ-2RKF1001X/) | ERJ-2RKF1001X (https://www.mouser.de/datasheet/2/315/AOA0000C304-1149620.pdf)
R109 | 100K | ERJ-2RKF1003X | 0402_R | Standard 0402 Resistor with American Symbol | ERJ-2RKF1003X (https://www.mouser.de/ProductDetail/Panasonic/ERJ-2RKF1003X/?qs=sGAEpiMZZMtlubZbdhIBIHcx2Q2RnT7K1YMPDp9rJM8%3D) | ERJ-2RKF1003X (https://www.mouser.de/datasheet/2/315/AOA0000C304-1149620.pdf)
R110 | 100K | ERJ-2RKF1003X | 0402_R | Standard 0402 Resistor with American Symbol | ERJ-2RKF1003X (https://www.mouser.de/ProductDetail/Panasonic/ERJ-2RKF1003X/?qs=sGAEpiMZZMtlubZbdhIBIHcx2Q2RnT7K1YMPDp9rJM8%3D) | ERJ-2RKF1003X (https://www.mouser.de/datasheet/2/315/AOA0000C304-1149620.pdf)
R111 | 100K | ERJ-2RKF1003X | 0402_R | Standard 0402 Resistor with American Symbol | ERJ-2RKF1003X (https://www.mouser.de/ProductDetail/Panasonic/ERJ-2RKF1003X/?qs=sGAEpiMZZMtlubZbdhIBIHcx2Q2RnT7K1YMPDp9rJM8%3D) | ERJ-2RKF1003X (https://www.mouser.de/datasheet/2/315/AOA0000C304-1149620.pdf)
R112 | TLR2HWDTE4L00F75 | TLR2HWDTE4L00F75 | TLR2HW | TLR2HB Current Sense Resistor Series | TLR2HWDTE4L00F75 (https://www.mouser.de/ProductDetail/KOA-Speer/TLR2HWDTE4L00F75/?qs=o%252BcmKBqJf7cmfbxuQONC%2FA==) | TLR2HWDTE4L00F75 (https://www.mouser.de/datasheet/2/219/TLR-2BW-2BP-2HW-3AP-3APS-1100841.pdf)
R113 | 31K6 | ERJ-2RKF3162X | 0402_R | Standard 0402 Resistor with American Symbol | ERJ-2RKF3162X (https://www.mouser.de/ProductDetail/Panasonic/ERJ-2RKF3162X/) | ERJ-2RKF3162X (https://www.mouser.de/datasheet/2/315/AOA0000C304-1149620.pdf)
R114 | 10K | ERJ-2RKF1002X | 0402_R | Standard 0402 Resistor with American Symbol | ERJ-2RKF1002X (https://www.mouser.de/ProductDetail/Panasonic/ERJ-2RKF1002X/?qs=H7k1u0Mp9JRzR4nj0ZFtQQ%3D%3D) | ERJ-2RKF1002X (https://www.mouser.de/datasheet/2/315/AOA0000C304-1149620.pdf)
R115 | 100K | ERJ-2RKF1003X | 0402_R | Standard 0402 Resistor with American Symbol | ERJ-2RKF1003X (https://www.mouser.de/ProductDetail/Panasonic/ERJ-2RKF1003X/?qs=sGAEpiMZZMtlubZbdhIBIHcx2Q2RnT7K1YMPDp9rJM8%3D) | ERJ-2RKF1003X (https://www.mouser.de/datasheet/2/315/AOA0000C304-1149620.pdf)
R116 | 10 | ERJ-2RKF10R0X | 0402_R | Standard 0402 Resistor with American Symbol | ERJ-2RKF10R0X (https://www.mouser.de/ProductDetail/Panasonic/ERJ-2RKF10R0X/) | ERJ-2RKF10R0X (https://www.mouser.de/datasheet/2/315/AOA0000C304-1149620.pdf)
R117 | 10 | ERJ-2RKF10R0X | 0402_R | Standard 0402 Resistor with American Symbol | ERJ-2RKF10R0X (https://www.mouser.de/ProductDetail/Panasonic/ERJ-2RKF10R0X/) | ERJ-2RKF10R0X (https://www.mouser.de/datasheet/2/315/AOA0000C304-1149620.pdf)
R118 | 220 | ERJ-2RKF2200X | 0402_R | Standard 0402 Resistor with American Symbol | ERJ-2RKF2200X (https://www.mouser.de/ProductDetail/Panasonic/ERJ-2RKF2200X/) | ERJ-2RKF2200X (https://www.mouser.de/datasheet/2/315/AOA0000C304-1149620.pdf)
R119 | 100K | ERJ-2RKF1003X | 0402_R | Standard 0402 Resistor with American Symbol | ERJ-2RKF1003X (https://www.mouser.de/ProductDetail/Panasonic/ERJ-2RKF1003X/?qs=sGAEpiMZZMtlubZbdhIBIHcx2Q2RnT7K1YMPDp9rJM8%3D) | ERJ-2RKF1003X (https://www.mouser.de/datasheet/2/315/AOA0000C304-1149620.pdf)
R120 | 100K | ERJ-2RKF1003X | 0402_R | Standard 0402 Resistor with American Symbol | ERJ-2RKF1003X (https://www.mouser.de/ProductDetail/Panasonic/ERJ-2RKF1003X/?qs=sGAEpiMZZMtlubZbdhIBIHcx2Q2RnT7K1YMPDp9rJM8%3D) | ERJ-2RKF1003X (https://www.mouser.de/datasheet/2/315/AOA0000C304-1149620.pdf)
R121 | 1K | ERJ-2RKF1001X | 0402_R | Standard 0402 Resistor with American Symbol | ERJ-2RKF1001X (https://www.mouser.de/ProductDetail/Panasonic/ERJ-2RKF1001X/) | ERJ-2RKF1001X (https://www.mouser.de/datasheet/2/315/AOA0000C304-1149620.pdf)

OpenServoCAN_Ver_2_BOM_Power_Board_V_1_0_1

Part | Value | Device | Package | Description | Shopping Link | Datasheet
T101 | IAUZ40N06S5N050ATMA1 | IAUZ40N06S5N050ATMA1 | PG-TSDSON-8-33-INF | N-Channel 60 V OptiMOS™ | IAUZ40N06S5N050ATMA1 (https://www.mouser.de/ProductDetail/Infineon-Technologies/IAUZ40N06S5N050ATMA1/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) | IAUZ40N06S5N050ATMA1 (https://www.mouser.de/datasheet/2/196/Infineon-IAUZ40N06S5N050-DataSheet-v01_00-EN-1863873.pdf)
T102 | IAUZ40N06S5N050ATMA1 | IAUZ40N06S5N050ATMA1 | PG-TSDSON-8-33-INF | N-Channel 60 V OptiMOS™ | IAUZ40N06S5N050ATMA1 (https://www.mouser.de/ProductDetail/Infineon-Technologies/IAUZ40N06S5N050ATMA1/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) | IAUZ40N06S5N050ATMA1 (https://www.mouser.de/datasheet/2/196/Infineon-IAUZ40N06S5N050-DataSheet-v01_00-EN-1863873.pdf)
T103 | IAUZ40N06S5N050ATMA1 | IAUZ40N06S5N050ATMA1 | PG-TSDSON-8-33-INF | N-Channel 60 V OptiMOS™ | IAUZ40N06S5N050ATMA1 (https://www.mouser.de/ProductDetail/Infineon-Technologies/IAUZ40N06S5N050ATMA1/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) | IAUZ40N06S5N050ATMA1 (https://www.mouser.de/datasheet/2/196/Infineon-IAUZ40N06S5N050-DataSheet-v01_00-EN-1863873.pdf)
T104 | IAUZ40N06S5N050ATMA1 | IAUZ40N06S5N050ATMA1 | PG-TSDSON-8-33-INF | N-Channel 60 V OptiMOS™ | IAUZ40N06S5N050ATMA1 (https://www.mouser.de/ProductDetail/Infineon-Technologies/IAUZ40N06S5N050ATMA1/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) | IAUZ40N06S5N050ATMA1 (https://www.mouser.de/datasheet/2/196/Infineon-IAUZ40N06S5N050-DataSheet-v01_00-EN-1863873.pdf)
T105 | SIS443DN-T1-GE3 | SIS443DN-T1-GE3 | POWERPAK-1212-8-S | P-Channel 40 V (D-S) MOSFET | SIS443DN-T1-GE3 (https://www.mouser.de/ProductDetail/Vishay-Semiconductors/SIS443DN-T1-GE3/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) | SIS443DN-T1-GE3 (https://www.mouser.de/datasheet/2/427/sis443dn-1761575.pdf)
T106 | SIS443DN-T1-GE3 | SIS443DN-T1-GE3 | POWERPAK-1212-8-S | P-Channel 40 V (D-S) MOSFET | SIS443DN-T1-GE3 (https://www.mouser.de/ProductDetail/Vishay-Semiconductors/SIS443DN-T1-GE3/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) | SIS443DN-T1-GE3 (https://www.mouser.de/datasheet/2/427/sis443dn-1761575.pdf)
T107 | UMX1NFHATN | UMX1NFHATN | SC-70-6 | UMX1NFHA | UMX1NFHATN (https://www.mouser.de/ProductDetail/ROHM-Semiconductor/UMX1NFHATN/) | UMX1NFHATN (https://www.mouser.de/datasheet/2/348/umx1nfha-e-1872402.pdf)

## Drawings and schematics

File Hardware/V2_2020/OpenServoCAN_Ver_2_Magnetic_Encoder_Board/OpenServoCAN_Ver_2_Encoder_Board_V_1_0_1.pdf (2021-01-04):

A

A

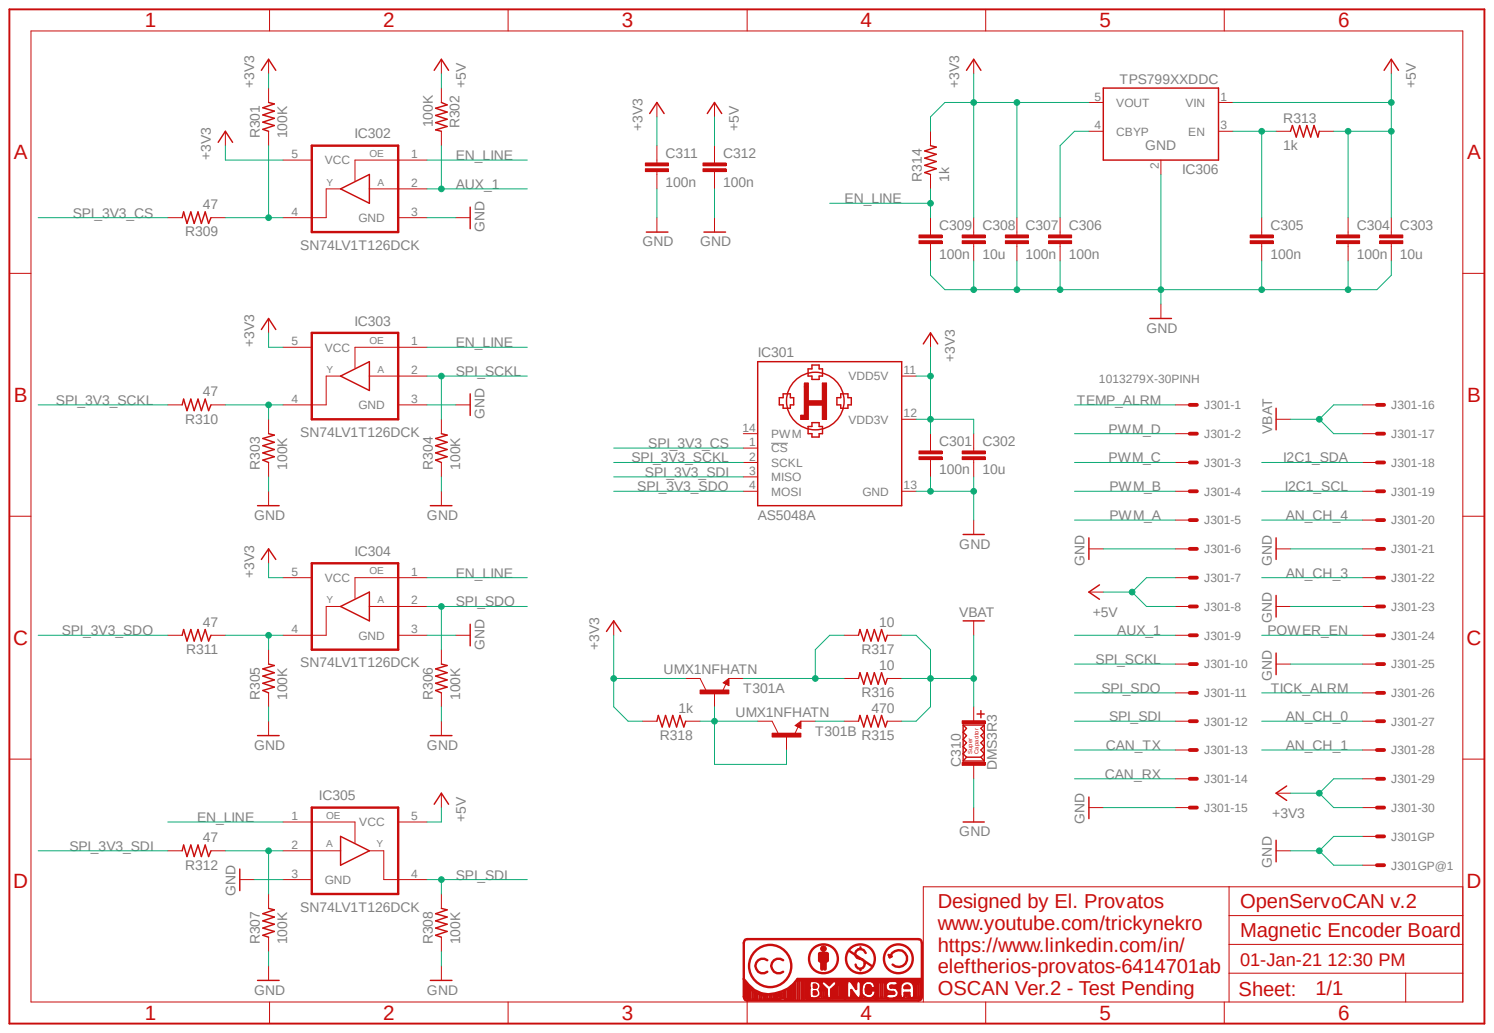
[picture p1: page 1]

GND GND

Designed by El. Provatos
www.youtube.com/trickynekro
https://www.linkedin.com/in/
eleftherios-provatos-6414701ab
OSCAN Ver.2 - Test Pending

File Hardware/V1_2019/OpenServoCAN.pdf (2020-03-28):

A

A

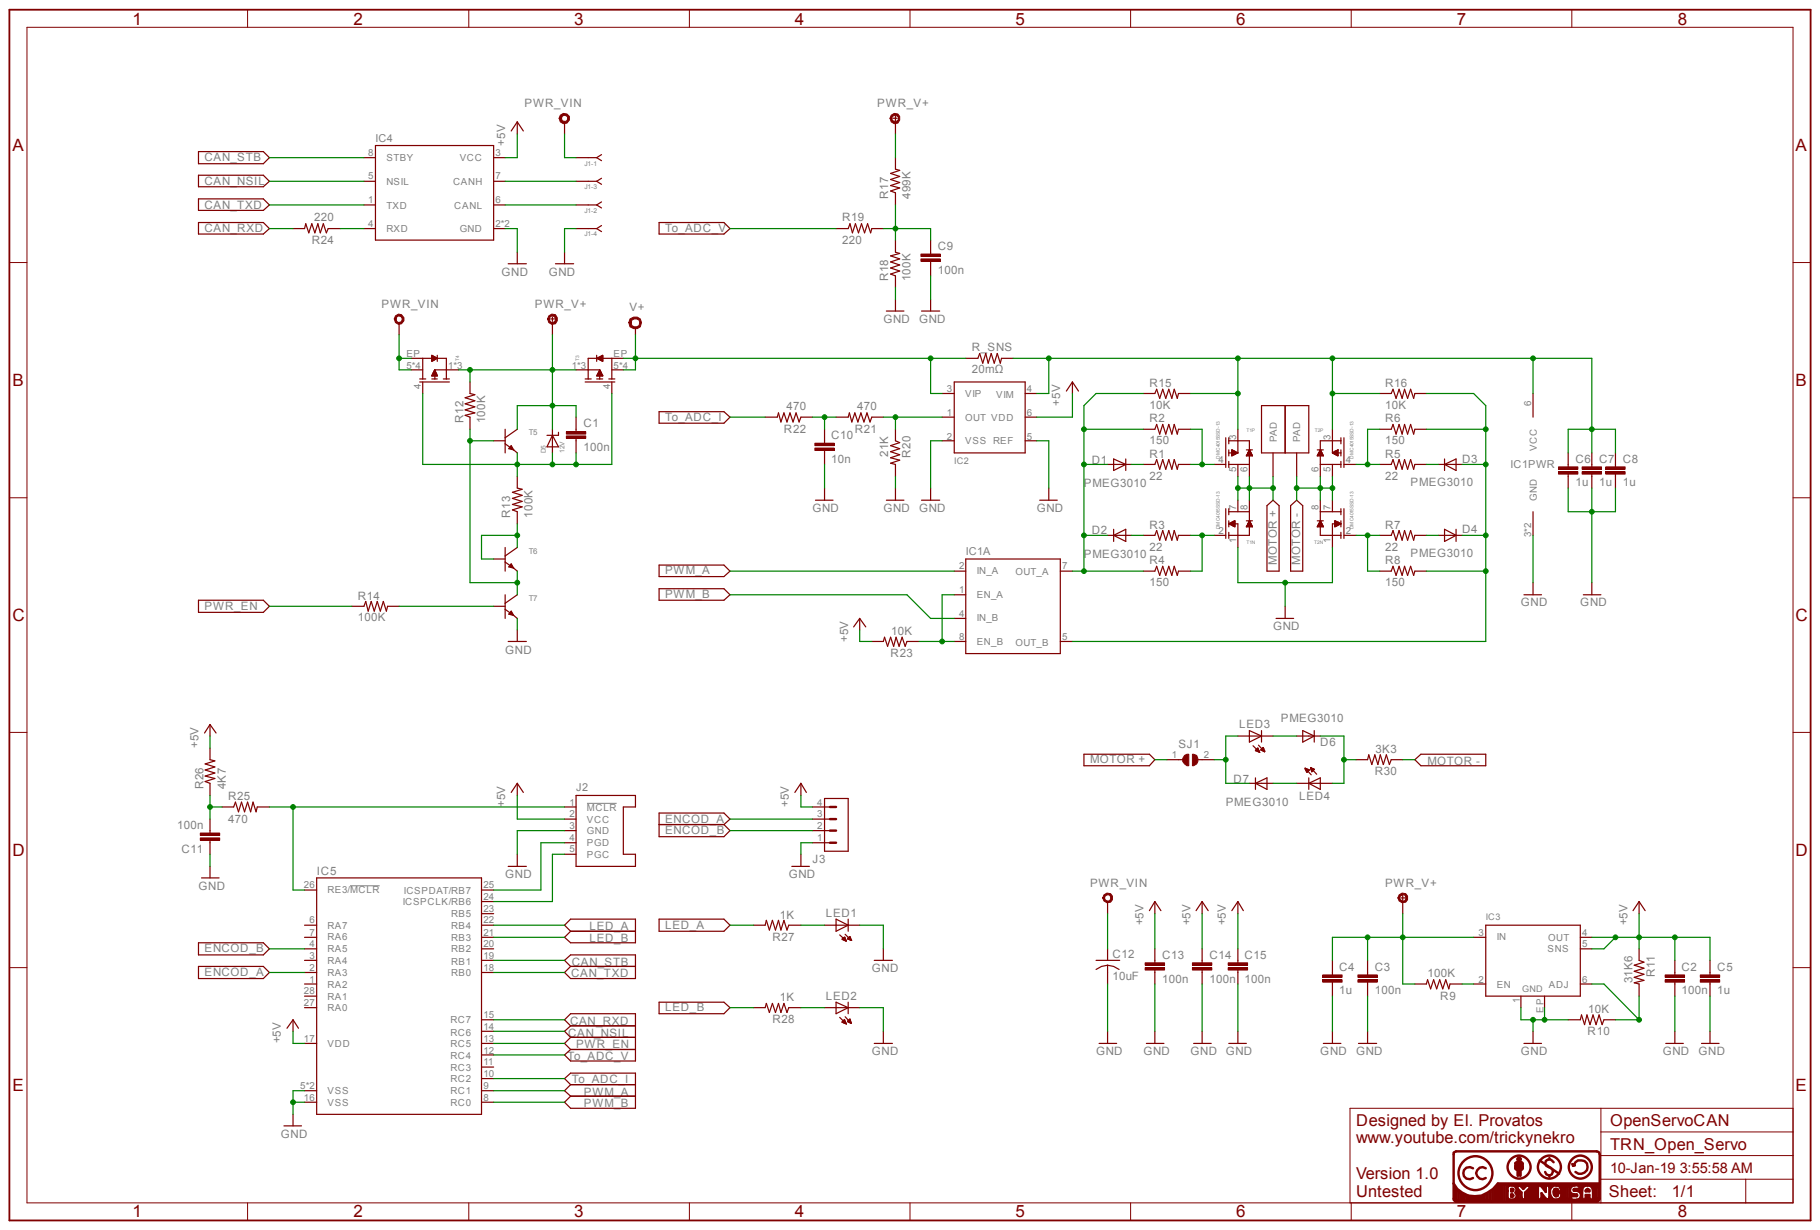
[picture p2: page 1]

www.youtube.com/trickynekro

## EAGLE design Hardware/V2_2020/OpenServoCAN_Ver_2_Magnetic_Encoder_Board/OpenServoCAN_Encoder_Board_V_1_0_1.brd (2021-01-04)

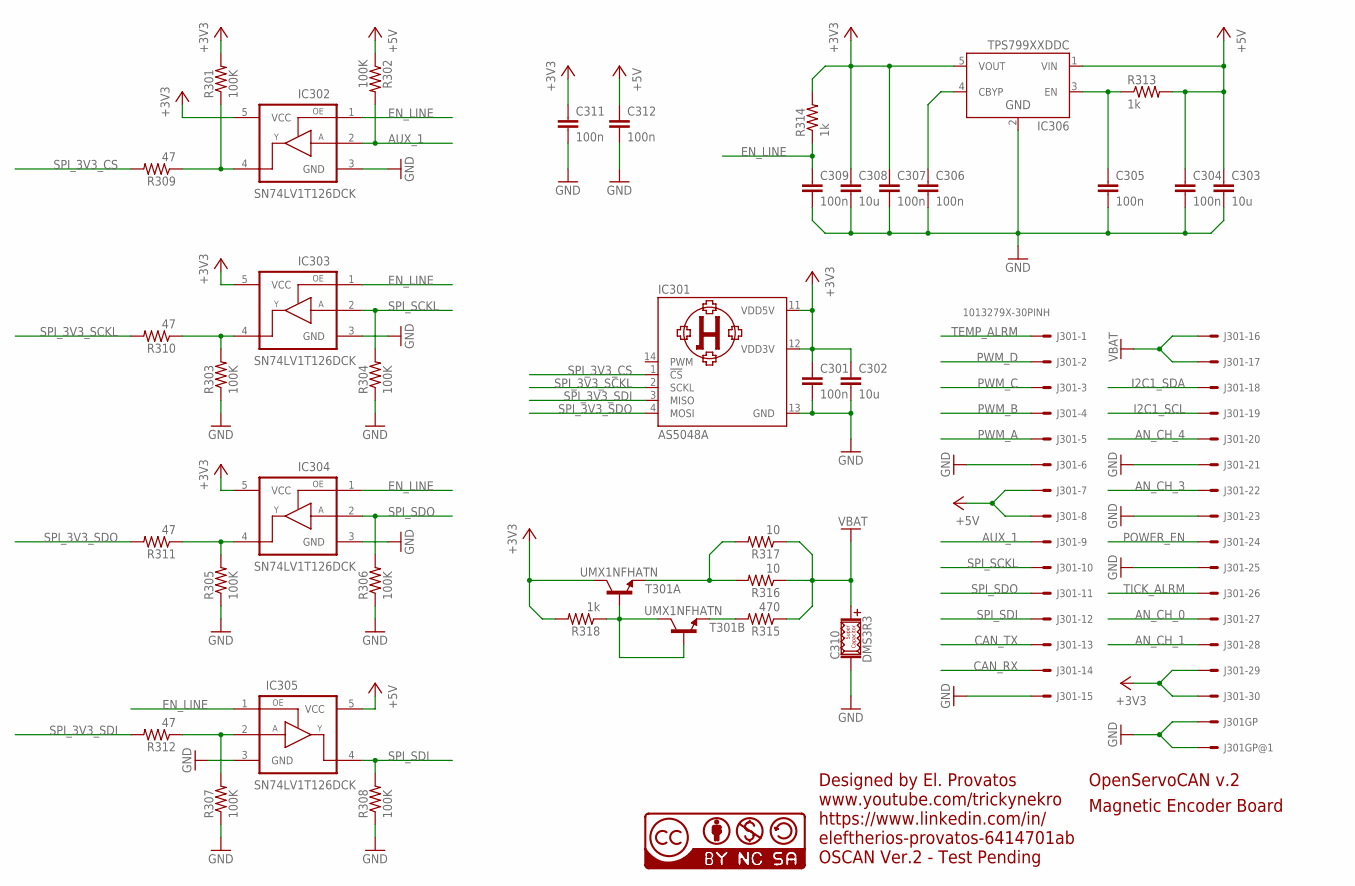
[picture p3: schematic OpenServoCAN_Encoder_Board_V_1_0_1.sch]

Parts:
C301, C304, C305, C306, C307, C309, C311, C312: 100n; 0402_C
C302, C303, C308: 10u; 0402_C
C310: DMS3R3; DMS_3R3_S_CAP
IC301: AS5048A; TSSOP-14
IC302, IC303, IC304, IC305: SN74LV1T126DCK; SC-70-5
IC306: TPS799XXDDC; SOT-23-5
J301: 1013279X-30PINH; 10132797-30
R301, R302, R303, R304, R305, R306, R307, R308: 100K; 0402_R
R309, R310, R311, R312: 47; 0402_R
R313, R314, R318: 1k; 0402_R
R315: 470; 0402_R
R316, R317: 10; 0402_R
T301: UMX1NFHATN; SC-70-6
U$1: CC-NC-BCNIX; CC-NC-B_NIX

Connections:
+3V3: C301.1, C302.1, C307.1, C308.1, C311.1, IC301.11 (VDD5V), IC301.12 (VDD3V), IC302.5 (VCC), IC303.5 (VCC), IC304.5 (VCC), IC306.5 (VOUT), J301.29, J301.30, R301.2, R314.2, R318.2, T301.6 (C)
+5V: C303.1, C304.1, C312.1, IC305.5 (VCC), IC306.1 (VIN), J301.7, J301.8, R302.1, R313.2
AN_CH_0: J301.27
AN_CH_1: J301.28
AN_CH_3: J301.22
AN_CH_4: J301.20
AUX_1: IC302.2 (A), J301.9, R302.2
CAN_RX: J301.14
CAN_TX: J301.13
EN_LINE: C309.1, IC302.1 (OE), IC303.1 (OE), IC304.1 (OE), IC305.1 (OE), R314.1
GND: C301.2, C302.2, C303.2, C304.2, C305.2, C306.2, C307.2, C308.2, C309.2, C310.NEG- (NEG), C311.2, C312.2, IC301.13 (GND), IC302.3 (GND), IC303.3 (GND), IC304.3 (GND), IC305.3 (GND), IC306.2 (GND), J301.6, J301.15, J301.21, J301.23, J301.25, J301.EP@2, J301.EP@↑1, R303.1, R304.1, R305.1, R306.1, R307.1, R308.1
I2C1_SCL: J301.19
I2C1_SDA: J301.18
unnamed: R318.1, T301.2 (B), T301.3 (C), T301.5 (B)
unnamed: C306.1, IC306.4 (CBYP)
unnamed: R316.2, R317.2, T301.1 (E)
unnamed: IC305.2 (A), R307.2, R312.1
unnamed: C305.1, IC306.3 (EN), R313.1
unnamed: IC304.4 (Y), R305.2, R311.1
unnamed: R315.2, T301.4 (E)
unnamed: IC303.4 (Y), R303.2, R310.1
unnamed: IC302.4 (Y), R301.1, R309.1
POWER_EN: J301.24
PWM_A: J301.5
PWM_B: J301.4
PWM_C: J301.3
PWM_D: J301.2
SPI_3V3_CS: IC301.1 (!CS), R309.2
SPI_3V3_SCKL: IC301.2 (SCKL), R310.2
SPI_3V3_SDI: IC301.3 (MISO), R312.2
SPI_3V3_SDO: IC301.4 (MOSI), R311.2
SPI_SCKL: IC303.2 (A), J301.10, R304.2
SPI_SDI: IC305.4 (Y), J301.12, R308.2
SPI_SDO: IC304.2 (A), J301.11, R306.2
TEMP_ALRM: J301.1
TICK_ALRM: J301.26
VBAT: C310.POS+ (POS), J301.16, J301.17, R315.1, R316.1, R317.1

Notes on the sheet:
OpenServoCAN v.2
Magnetic Encoder Board
Designed by El. Provatos
www.youtube.com/trickynekro
https://www.linkedin.com/in/ eleftherios-provatos-6414701ab
OSCAN Ver.2 - Test Pending

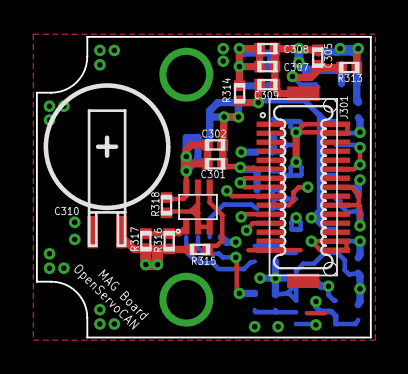
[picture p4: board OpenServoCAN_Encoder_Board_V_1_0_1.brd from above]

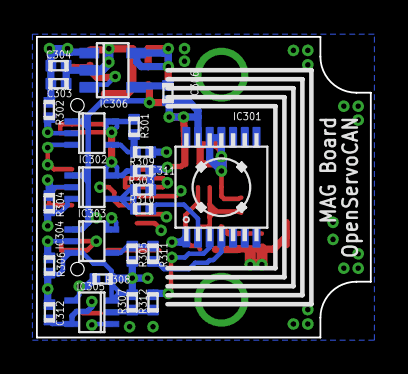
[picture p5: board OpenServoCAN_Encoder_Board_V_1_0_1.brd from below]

Board: 4 copper layers, 18.6 x 16.7 mm, 39 parts (23 on the bottom side), 22 nets.

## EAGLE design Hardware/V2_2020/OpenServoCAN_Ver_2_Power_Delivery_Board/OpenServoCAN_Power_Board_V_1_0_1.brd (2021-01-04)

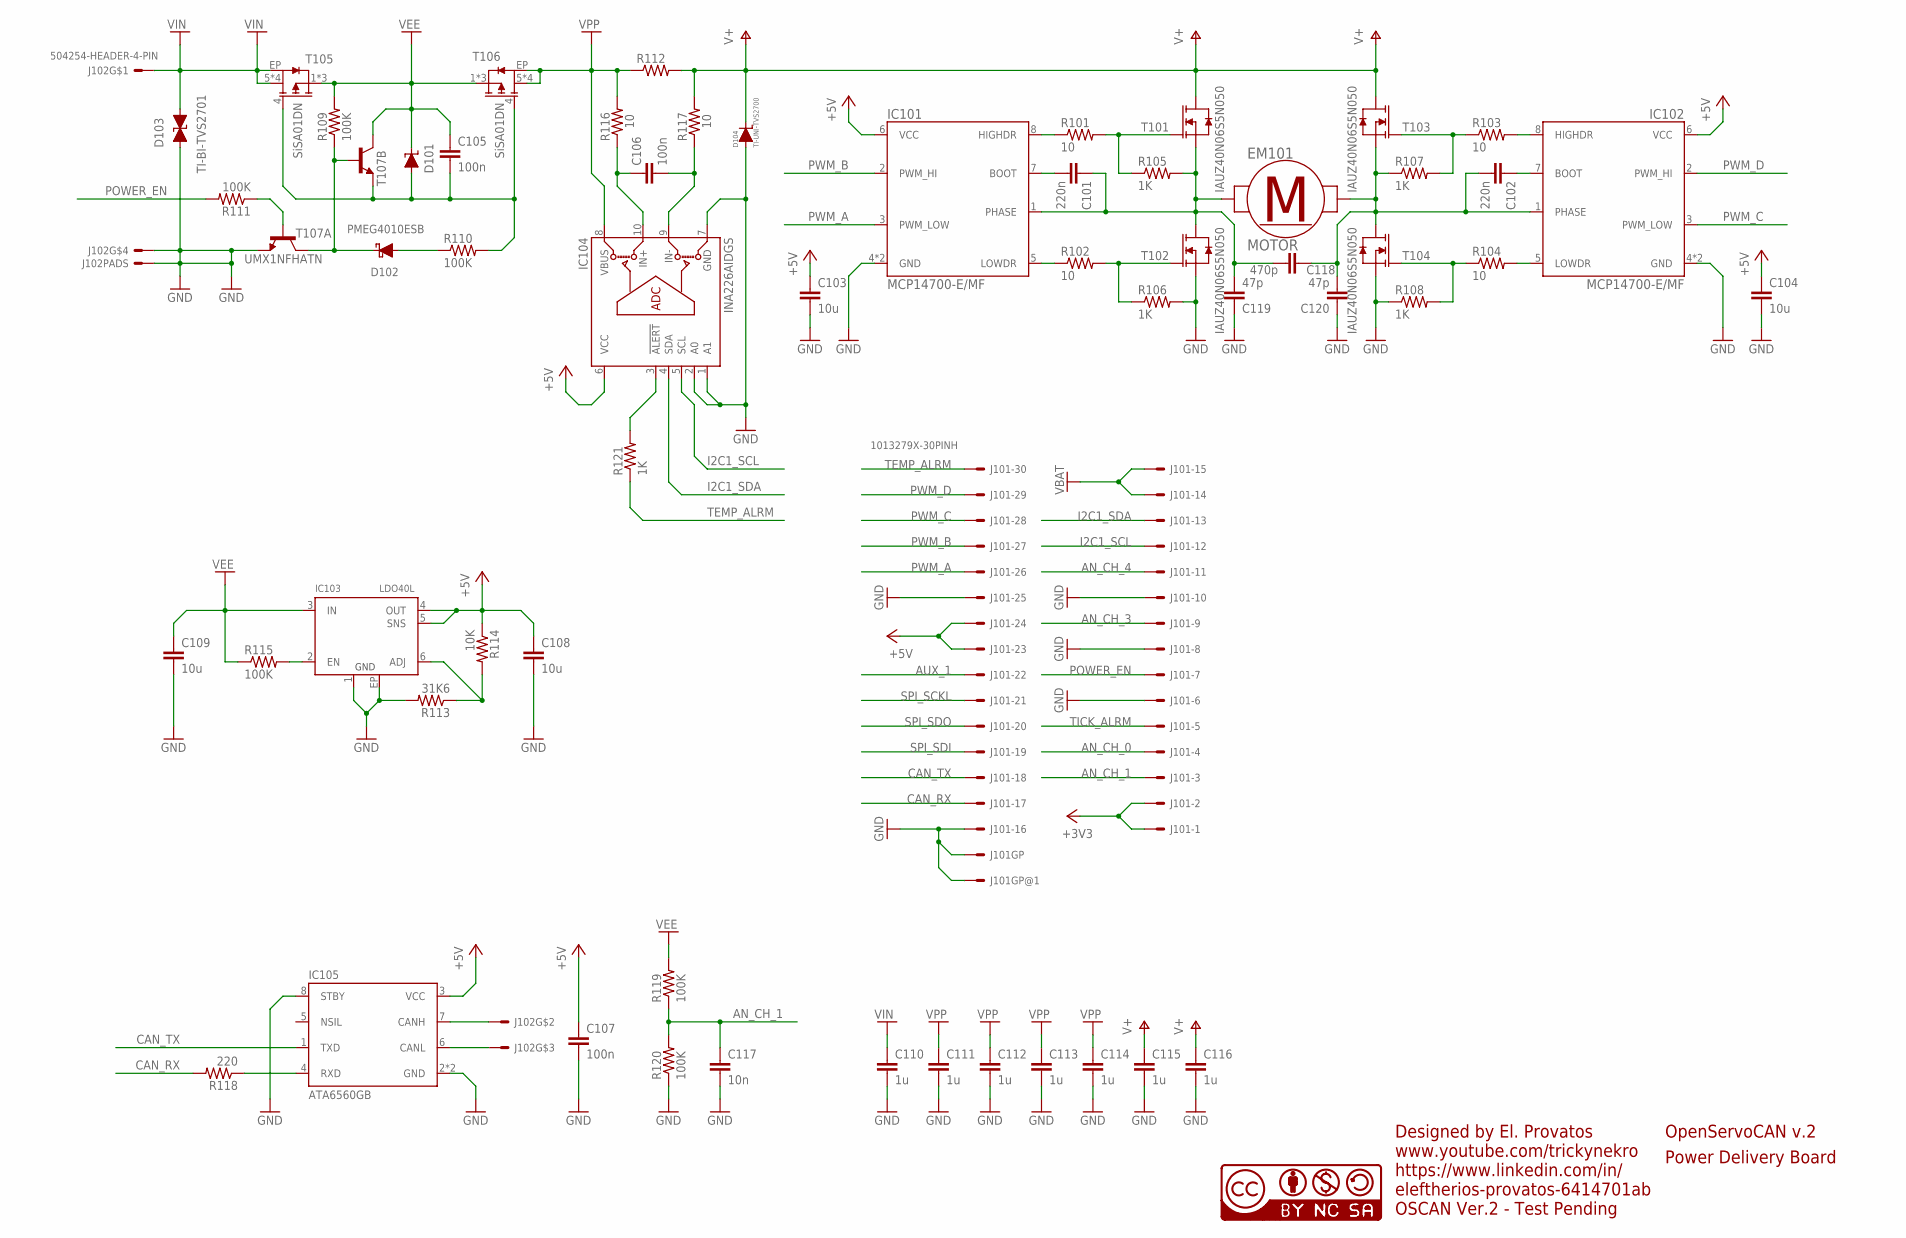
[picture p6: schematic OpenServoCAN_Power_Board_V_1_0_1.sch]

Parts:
C101, C102: 220n; 0603_C
C103, C104, C108, C109: 10u; 0402_C
C105, C106, C107: 100n; 0402_C
C110, C111, C112, C113, C114, C115, C116: 1u; 0603_C
C117: 10n; 0402_C
C118: 470p; 1206_C
C119, C120: 47p; 1206_C
D101: DDZ12CSF; SOD-323
D102: PMEG4010ESB; DSN1006-2
D103: TI-BI-TVS2701; VSON-8-DRB0008A
D104: TI-UNI-TVS2700; WSON-6
EM101: MOTOR; RF-020TH-10210
IC101, IC102: MCP14700-E/MF; DFN_8_3X3X09_MF_MICROCHIP
IC103: LDO40L; DFN6-3X3
IC104: INA226AIDGS; VSSOP-10
IC105: ATA6560GB; VDFN-8-EP
J101: 1013279X-30PINH; 10132797-30
J102: 504254-HEADER-4-PIN; 504254
R101, R102, R103, R104, R116, R117: 10; 0402_R
R105, R106, R107, R108, R121: 1K; 0402_R
R109, R110, R111, R115, R119, R120: 100K; 0402_R
R112: TLR2HW-R-US-SENSE; TLR2HW
R113: 31K6; 0402_R
R114: 10K; 0402_R
R118: 220; 0402_R
T101, T102, T103, T104: IAUZ40N06S5N050; PG-TSDSON-8-33-INF
T105, T106: SiSA01DN; POWERPAK-1212-8-SINGLE
T107: UMX1NFHATN; SC-70-6
U$1: CC-NC-BCNIX; CC-NC-B_NIX

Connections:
+3V3: J101.1, J101.2
+5V: C103.1, C104.1, C107.1, C108.1, IC101.6 (VCC), IC102.6 (VCC), IC103.4 (OUT), IC103.5 (SNS), IC104.6 (VCC), IC105.3 (VCC), J101.23, J101.24, R114.1
AN_CH_0: J101.4
AN_CH_1: C117.1, J101.3, R119.1, R120.2
AN_CH_3: J101.9
AN_CH_4: J101.11
AUX_1: J101.22
CAN_RX: J101.17, R118.2
CAN_TX: IC105.1 (TXD), J101.18
GND: C103.2, C104.2, C107.2, C108.2, C109.2, C110.2, C111.2, C112.2, C113.2, C114.2, C115.2, C116.2, C117.2, C119.1, C120.1, D103.5 (A), D103.6 (A), D103.7 (A), D103.8 (A), D104.1 (A), D104.2 (A), D104.3 (A), D104.EP (A), IC101.4 (GND), IC101.EP (GND), IC102.4 (GND), IC102.EP (GND), IC103.1 (GND), IC103.EP (GND), IC104.1 (A1), IC104.2 (A0), IC104.7 (GND), IC105.2 (GND), IC105.8 (STBY), IC105.EP (GND), J101.6, J101.8, J101.10, J101.16, J101.25, J101.EP@2, J101.EP@↑1, J102.4, J102.EP@1, J102.EP@2, J102.EP@3, J102.EP@4, R106.2, R108.1, R113.2, R120.1, T102.S, T104.S, T107.1 (E)
I2C1_SCL: IC104.5 (SCL), J101.12
I2C1_SDA: IC104.4 (SDA), J101.13
unnamed: C101.1, C118.2, C119.2, EM101.1B (1), EM101.1T (1), IC101.1 (PHASE), R105.2, T101.S, T102.D
unnamed: C102.2, C118.1, C120.2, EM101.2B (2), EM101.2T (2), IC102.1 (PHASE), R107.1, T103.S, T104.D
unnamed: R103.1, R107.2, T103.G
unnamed: IC101.8 (HIGHDR), R101.1
unnamed: R101.2, R105.1, T101.G
unnamed: IC102.8 (HIGHDR), R103.2
unnamed: IC104.3 (!ALERT), R121.2
unnamed: R102.2, R106.1, T102.G
unnamed: IC101.5 (LOWDR), R102.1
unnamed: R104.1, R108.2, T104.G
unnamed: IC102.5 (LOWDR), R104.2
unnamed: C102.1, IC102.7 (BOOT)
unnamed: IC103.6 (ADJ), R113.1, R114.2
unnamed: C101.2, IC101.7 (BOOT)
unnamed: IC103.2 (EN), R115.2
unnamed: C106.1, IC104.10 (IN+), R116.1
unnamed: C106.2, IC104.9 (IN-), R117.1
unnamed: IC105.7 (CANH), J102.2
unnamed: IC105.6 (CANL), J102.3
unnamed: D102.K, R109.1, T107.5 (B), T107.6 (C)
unnamed: D102.A, R110.1
unnamed: C105.2, D101.A, R110.2, T105.4 (G), T106.4 (G), T107.4 (E)
unnamed: R111.1, T107.2 (B)
unnamed: IC105.4 (RXD), R118.1
POWER_EN: J101.7, R111.2
PWM_A: IC101.3 (PWM_LOW), J101.26
PWM_B: IC101.2 (PWM_HI), J101.27
PWM_C: IC102.3 (PWM_LOW), J101.28
PWM_D: IC102.2 (PWM_HI), J101.29
SPI_SCKL: J101.21
SPI_SDI: J101.19
SPI_SDO: J101.20
TEMP_ALRM: J101.30, R121.1
TICK_ALRM: J101.5
V+: C115.1, C116.1, D104.4 (K), D104.5 (K), D104.6 (K), R112.2, R117.2, T101.D, T103.D
VBAT: J101.14, J101.15
VEE: C105.1, C109.1, D101.K, IC103.3 (IN), R109.2, R115.1, R119.2, T105.1 (S), T105.2 (S), T105.3 (S), T106.1 (S), T106.2 (S), T106.3 (S), T107.3 (C)
VIN: C110.1, D103.1 (K), D103.2 (K), D103.3 (K), D103.4 (K), J102.1, T105.5 (D), T105.6 (D), T105.7 (D), T105.8 (D), T105.EP (D)
VPP: C111.1, C112.1, C113.1, C114.1, IC104.8 (VBUS), R112.1, R116.2, T106.5 (D), T106.6 (D), T106.7 (D), T106.8 (D), T106.EP (D)

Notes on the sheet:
Designed by El. Provatos
www.youtube.com/trickynekro
https://www.linkedin.com/in/ eleftherios-provatos-6414701ab
OSCAN Ver.2 - Test Pending
OpenServoCAN v.2
Power Delivery Board

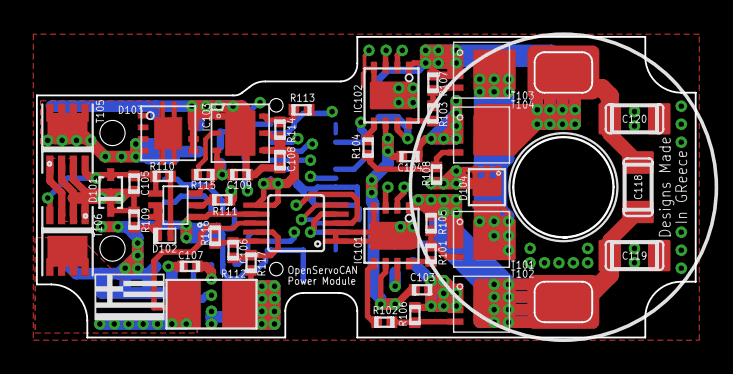
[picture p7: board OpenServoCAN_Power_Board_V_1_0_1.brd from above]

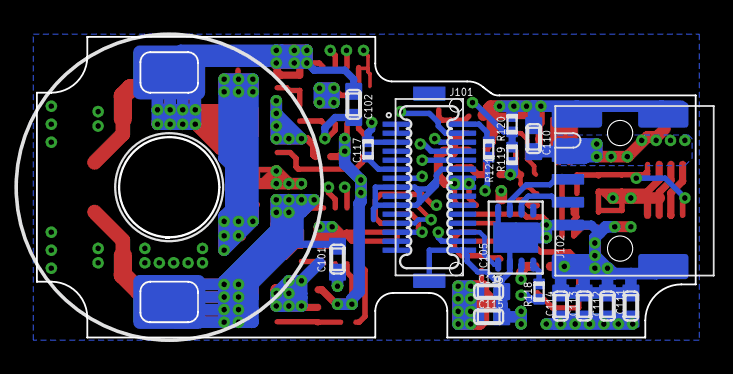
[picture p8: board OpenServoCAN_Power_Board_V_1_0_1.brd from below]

Board: 4 copper layers, 36.6 x 16.7 mm, 61 parts (18 on the bottom side), 43 nets.

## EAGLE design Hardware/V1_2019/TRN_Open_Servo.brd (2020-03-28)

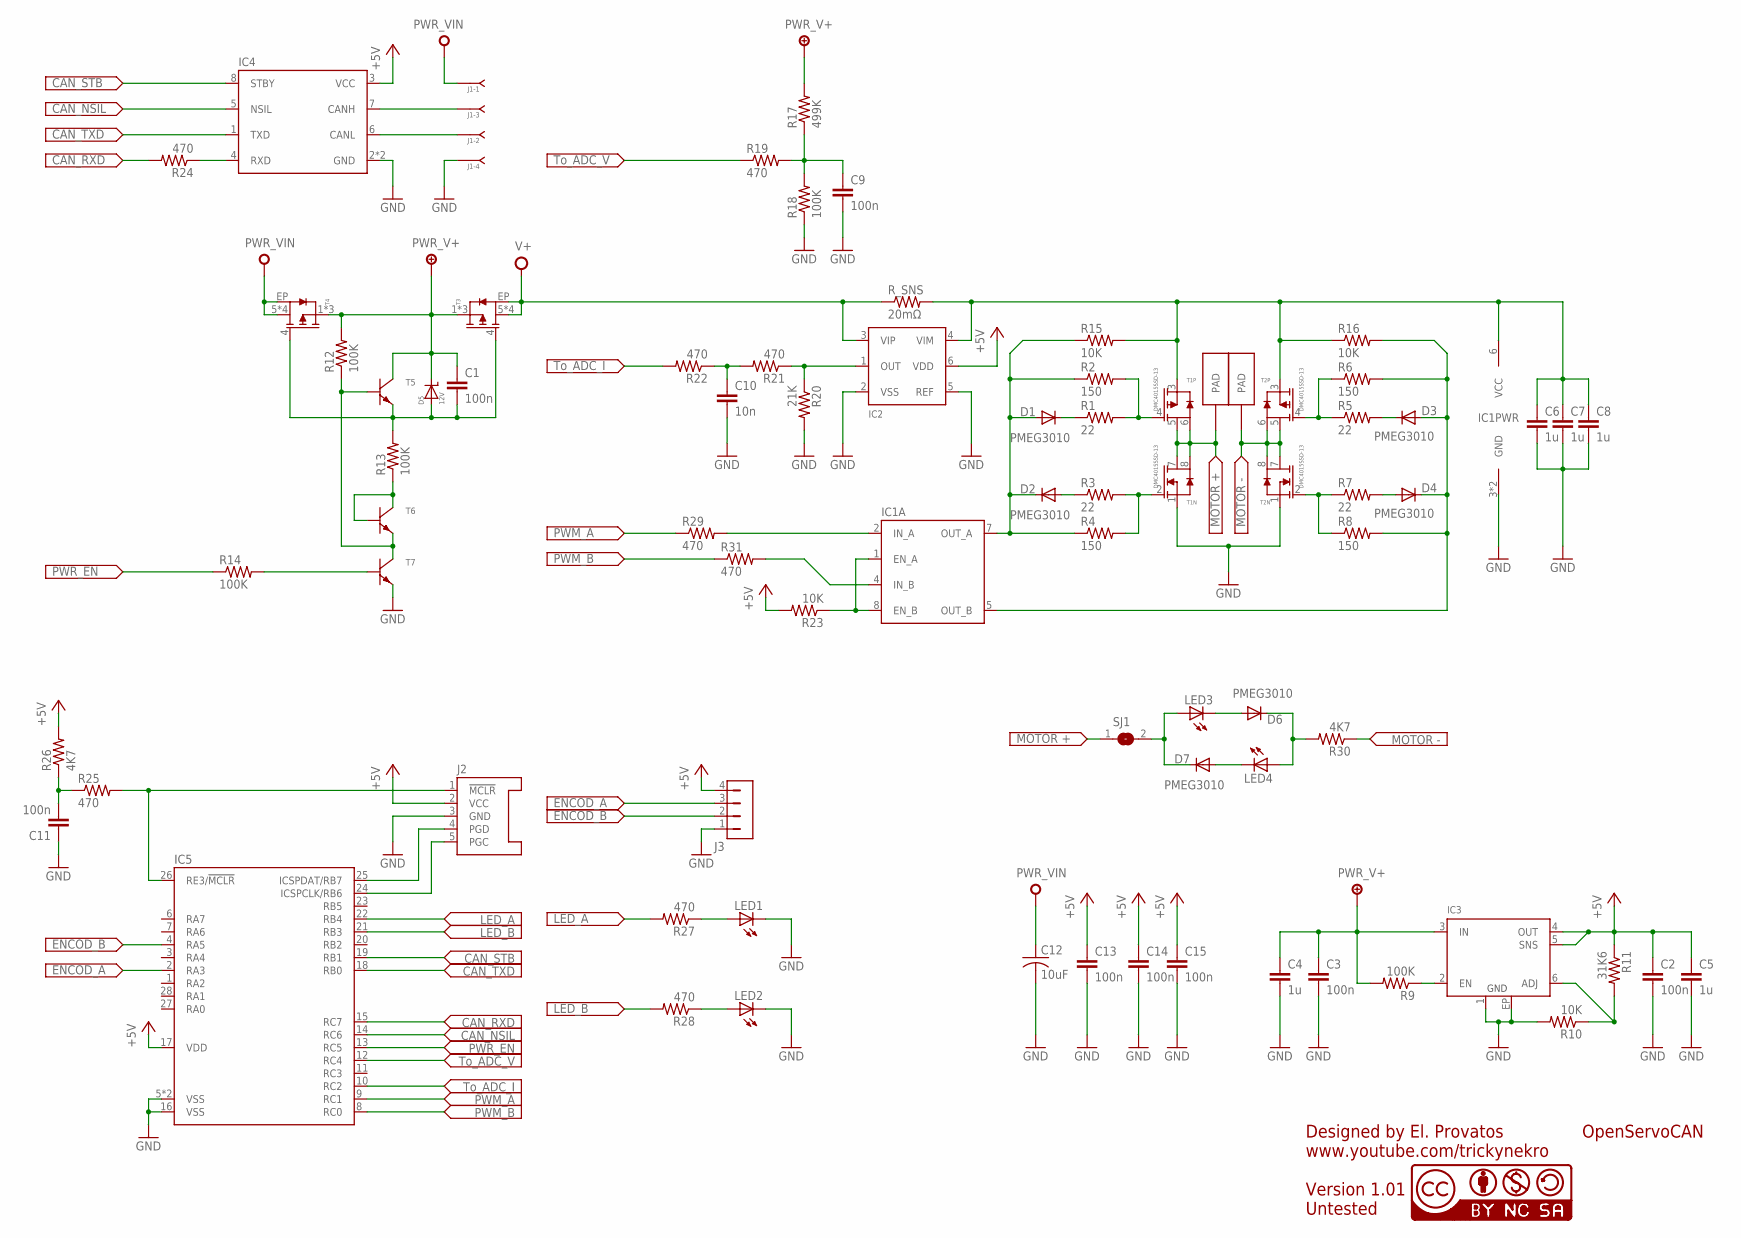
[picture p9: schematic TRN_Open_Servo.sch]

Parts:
C1, C2, C3, C9, C11, C13, C14, C15: 100n; C0402
C4, C5, C6, C7, C8: 1u; C0603K
C10: 10n; C0402
C12: 10uF; C1210
D1, D2, D3, D4, D6, D7: PMEG3010; SOD523
D5: 12V; SOD-323
IC1: MCP14A0454MNY; TDFN-8-EP
IC2: MCP6C02SMD; SOT-23-6
IC3: LDO40L-ADJ; DFN6-3X3
IC4: ATA6560GB; VDFN-8-EP
IC5: PIC18F26K83ML; QFN-28
J1: J-04-SIP-100; SIP-100-04
J2: PIC-ICSP-MICRO; PICOBLADE-5
J3: 1X4_PICOBLADE_CONNECTOR; PICOBLADE-4
LED1, LED2, LED3, LED4: LEDCHIP-LED0603; CHIP-LED0603
PAD1, PAD2: PLATED_SLOT
R1, R3, R5, R7: 22; R0402
R2, R4, R6, R8: 150; R0402
R9, R12, R13, R14, R18: 100K; R0402
R10, R15, R16, R23: 10K; R0402
R11: 31K6; R0402
R17: 499K; R0402
R19, R21, R22, R24, R25, R27, R28, R29, R31: 470; R0402
R20: 21K; R0402
R26, R30: 4K7; R0402
R_SNS: 20mΩ; R0805
SJ1: SJ
T1, T2: DMC4015SSD-13; SO-8
T3, T4: SISA01DN; POWERPAK-1212-8
T5, T6, T7: MMBT2222AM3T5G; SOT-723-3
U$1: CC-NC-BCNIX; CC-NC-B_NIX

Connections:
+5V: C2.1, C5.1, C13.1, C14.1, C15.1, IC2.6 (VDD), IC3.4 (OUT), IC3.5 (SNS), IC4.3 (VCC), IC5.17 (VDD), J2.2 (VCC), J3.4, R11.1, R23.2, R26.2
CAN_NSIL: IC4.5 (NSIL), IC5.14 (RC6)
CAN_RXD: IC5.15 (RC7), R24.2
CAN_STB: IC4.8 (STBY), IC5.19 (RB1)
CAN_TXD: IC4.1 (TXD), IC5.18 (RB0)
ENCOD_A: IC5.2 (RA3), J3.3
ENCOD_B: IC5.4 (RA5), J3.2
GND: C2.2, C3.2, C4.2, C5.2, C6.2, C7.2, C8.2, C9.2, C10.2, C11.1, C12.2, C13.2, C14.2, C15.2, IC1.3 (GND), IC1.EP (GND), IC2.2 (VSS), IC2.5 (REF), IC3.1 (GND), IC3.EP (GND), IC4.2 (GND), IC4.EP (GND), IC5.5 (VSS), IC5.16 (VSS), IC5.EP (VSS), J1.4, J2.3 (GND), J3.1, LED1.C, LED2.C, R10.2, R18.1, R20.2, T1.1 (S), T2.1 (S), T7.2 (E)
LED_A: IC5.22 (RB4), R27.2
LED_B: IC5.21 (RB3), R28.2
MOTOR+: PAD1.P$1, PAD1.P$2, SJ1.1, T1.5 (D), T1.6 (D), T1.7 (D), T1.8 (D)
MOTOR-: PAD2.P$1, PAD2.P$2, R30.1, T2.5 (D), T2.6 (D), T2.7 (D), T2.8 (D)
unnamed: D7.C, LED3.A, SJ1.2
unnamed: IC3.2 (EN), R9.1
unnamed: D6.C, LED4.A, R30.2
unnamed: D3.A, D4.C, IC1.5 (OUT_B), R6.2, R8.2, R16.2
unnamed: D1.A, D2.C, IC1.7 (OUT_A), R2.1, R4.1, R15.1
unnamed: D1.C, R1.1
unnamed: R1.2, R2.2, T1.4 (G)
unnamed: R3.2, R4.2, T1.2 (G)
unnamed: D2.A, R3.1
unnamed: D3.C, R5.2
unnamed: R5.1, R6.1, T2.4 (G)
unnamed: R7.1, R8.1, T2.2 (G)
unnamed: D4.A, R7.2
unnamed: IC3.6 (ADJ), R10.1, R11.2
unnamed: C6.1, C7.1, C8.1, IC1.6 (VCC), IC2.4 (VIM), R15.2, R16.1, R_SNS.2, T1.3 (S), T2.3 (S)
unnamed: R12.1, T5.1 (B), T6.2 (E), T7.3 (C)
unnamed: IC4.7 (CANH), J1.3
unnamed: C1.2, D5.A, R13.2, T3.4 (G), T4.4 (G), T5.2 (E)
unnamed: R13.1, T6.1 (B), T6.3 (C)
unnamed: IC4.6 (CANL), J1.2
unnamed: C9.1, R17.1, R18.2, R19.2
unnamed: IC1.1 (EN_A), IC1.8 (EN_B), R23.1
unnamed: R14.2, T7.1 (B)
unnamed: IC5.26 (RE3/!MCLR!), J2.1 (!MCLR), R25.2
unnamed: C11.2, R25.1, R26.1
unnamed: LED1.A, R27.1
unnamed: IC2.1 (OUT), R20.1, R21.1
unnamed: IC5.24 (ICSPCLK/RB6), J2.5 (PGC)
unnamed: IC5.25 (ICSPDAT/RB7), J2.4 (PGD)
unnamed: C10.1, R21.2, R22.1
unnamed: IC4.4 (RXD), R24.1
unnamed: D6.A, LED3.C
unnamed: D7.A, LED4.C
unnamed: LED2.A, R28.1
unnamed: IC1.2 (IN_A), R29.2
unnamed: IC1.4 (IN_B), R31.2
PWM_A: IC5.9 (RC1), R29.1
PWM_B: IC5.8 (RC0), R31.1
PWR_EN: IC5.13 (RC5), R14.1
PWR_V+: C1.1, C3.1, C4.1, D5.K, IC3.3 (IN), R9.2, R12.2, R17.2, T3.1 (S), T3.2 (S), T3.3 (S), T4.1 (S), T4.2 (S), T4.3 (S), T5.3 (C)
PWR_VIN: C12.1, J1.1, T4.5 (D), T4.6 (D), T4.7 (D), T4.8 (D), T4.EP (D)
TO_ADC_I: IC5.10 (RC2), R22.2
TO_ADC_V: IC5.12 (RC4), R19.1
V+: IC2.3 (VIP), R_SNS.1, T3.5 (D), T3.6 (D), T3.7 (D), T3.8 (D), T3.EP (D)

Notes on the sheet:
OpenServoCAN
Designed by El. Provatos
Version 1.01
www.youtube.com/trickynekro
Untested

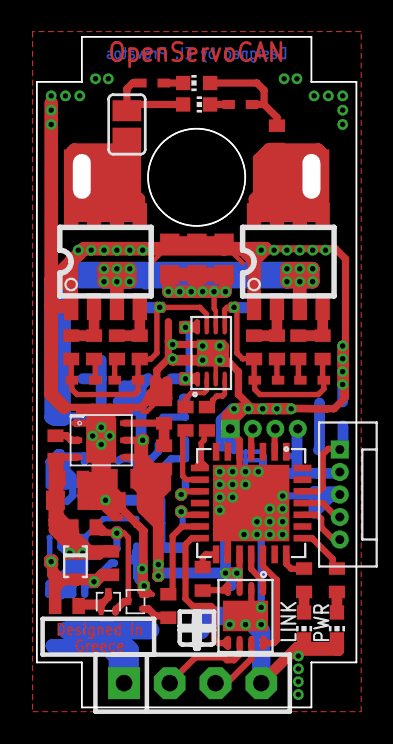
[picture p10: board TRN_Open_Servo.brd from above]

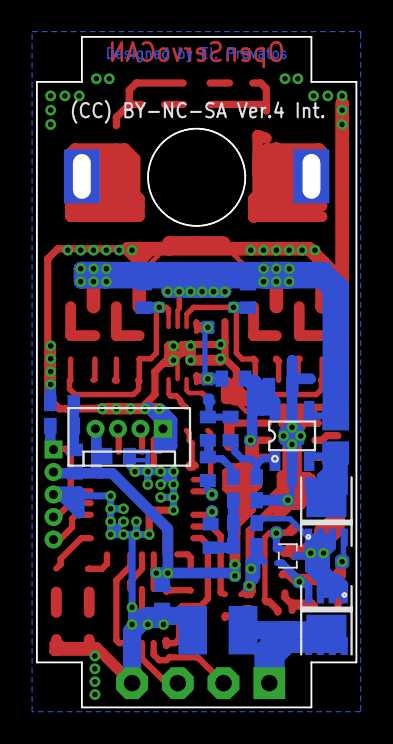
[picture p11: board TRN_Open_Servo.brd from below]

Board: 2 copper layers, 17.8 x 37.2 mm, 77 parts (24 on the bottom side), 56 nets.

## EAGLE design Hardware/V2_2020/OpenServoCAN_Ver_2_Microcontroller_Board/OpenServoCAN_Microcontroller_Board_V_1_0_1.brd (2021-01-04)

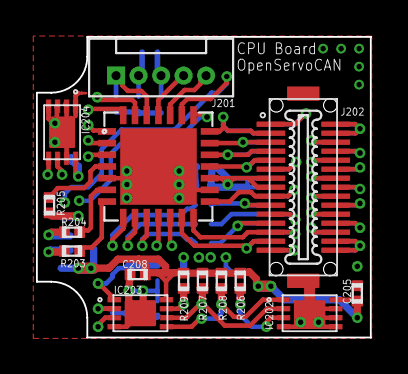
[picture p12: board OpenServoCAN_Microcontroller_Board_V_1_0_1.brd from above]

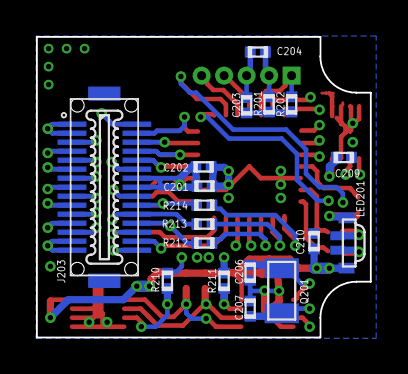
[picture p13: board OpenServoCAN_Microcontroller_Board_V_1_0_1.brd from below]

Board: 4 copper layers, 18.6 x 16.7 mm, 35 parts (18 on the bottom side), 40 nets.

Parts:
C201, C203, C204, C205, C208, C209, C210: 100n; 0402_C
C202: 2u2; 0402_C
C206, C207: 22p; 0402_C
IC201: QFN-28
IC202: MCP9808T-E/MC; DFN_2X3_MICROCHIP
IC203: MCP7940N; DFN_2X3_MICROCHIP
IC204: 24XX64MC; DFN_2X3_MICROCHIP
J201: PICOBLADE-5
J202, J203: 1013279X-30PINR; 10132798-30
LED201: 1206_RGB_LED
LOGO1: TRN_LOGO_INV; TRN_LOGO_2020_INV
Q201: LFXTAL009678
R201, R206, R207, R208, R209: 4k7; 0402_R
R202, R210, R211: 470; 0402_R
R203, R204, R205: 220; 0402_R
R212, R213, R214: 47; 0402_R
U$1: CC-NC-BCNIX; CC-NC-B_NIX

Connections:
+3V3: J202.29, J202.30, J203.1, J203.2
+5V: C201.1, C202.1, C204.1, C205.1, C208.1, C209.1, C210.1, IC201.17, IC202.8, IC203.8, IC204.8, J201.2, J202.7, J202.8, J203.23, J203.24, LED201.3, R201.2, R206.2, R207.2, R208.2, R209.2
AN_CH_0: IC201.27, J202.27, J203.4
AN_CH_1: IC201.28, J202.28, J203.3
AN_CH_3: IC201.2, J202.22, J203.9
AN_CH_4: IC201.3, J202.20, J203.11
AUX_1: IC201.15, J202.9, J203.22
CAN_RX: IC201.13, J202.14, J203.17
CAN_TX: IC201.14, J202.13, J203.18
GND: C201.2, C202.2, C203.2, C204.2, C205.2, C206.2, C207.2, C208.2, C209.2, C210.2, IC201.5, IC201.16, IC201.EP, IC202.4, IC202.5, IC202.6, IC202.7, IC202.EP, IC203.4, IC203.EP, IC204.1, IC204.2, IC204.3, IC204.4, IC204.7, IC204.EP, J201.3, J202.6, J202.15, J202.21, J202.23, J202.25, J202.EP@2, J202.EP@↑1, J203.6, J203.8, J203.10, J203.16, J203.25, J203.EP@2, J203.EP@↑1
I2C1_SCL: IC201.11, IC202.2, IC203.6, IC204.6, J202.19, J203.12, R207.1
I2C1_SDA: IC201.12, IC202.1, IC203.5, IC204.5, J202.18, J203.13, R208.1
LED_B: IC201.7, R203.2
LED_G: IC201.6, R204.2
LED_R: IC201.4, R205.2
unnamed: C203.1, R201.1, R202.2
unnamed: IC201.26, J201.1, R202.1
unnamed: IC201.24, J201.5
unnamed: IC202.3, R206.1, R210.1
unnamed: IC201.25, J201.4
unnamed: LED201.2, R204.1
unnamed: LED201.4, R205.1
unnamed: LED201.1, R203.1
unnamed: IC203.7, R209.1, R211.1
unnamed: C206.1, IC203.1, Q201.P$2
unnamed: C207.1, IC203.2, Q201.P$1
unnamed: IC201.10, R212.1
unnamed: IC201.9, R213.2
unnamed: IC201.8, R214.2
POWER_EN: IC201.1, J202.24, J203.7
PWM_A: IC201.18, J202.5, J203.26
PWM_B: IC201.19, J202.4, J203.27
PWM_C: IC201.20, J202.3, J203.28
PWM_D: IC201.21, J202.2, J203.29
SPI_SCKL: J202.10, J203.21, R214.1
SPI_SDI: J202.12, J203.19, R212.2
SPI_SDO: J202.11, J203.20, R213.1
TEMP_ALRM: IC201.23, J202.1, J203.30, R210.2
TICK_ALRM: IC201.22, J202.26, J203.5, R211.2
VBAT: IC203.3, J202.16, J202.17, J203.14, J203.15

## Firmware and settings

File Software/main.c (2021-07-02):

/* 
 * File:   main.c
 * Author: El. Pro @ TrickyNekro
 *
 * Created on July 8, 2019, 11:26 PM
 */

#define _XTAL_FREQ         64000000L
#define C_STEP             5
#define PWM_LIM            1023


#include <xc.h>
#include <stdio.h>
#include <stdlib.h>
#include <stdbool.h>

#include "configuration_pins.h"
#include "Timer_2.h"
#include "Timer_4.h"
#include "Timer_6.h"
#include "PWM5_Module.h"
#include "PWM6_Module.h"
#include "PWM7_Module.h"
#include "PWM8_Module.h"

/*
 * 
 */
int main(void)
{
    // Initialize the Pins of the Microcontroller 
    PINS_Direction_Configure_Active ( );
    
    // Disable all LED pins
    LATAbits.LATA7 = 1;
    LATAbits.LATA6 = 1;
    LATAbits.LATA5 = 1;
    
    // Initialize the Peripheral connections to Pins
    PINS_Peripherals_Configure_Active ( );
    // Initialize Timer 2
    Timer_2_Configure ( T2CON_CKPS_PRESC_1_2, T2CON_OUTPS_POST_1_1, 
                        T2CKL_CS_F_OSC_DIV_4, TMR2_PERIOD_MAX, 
                        T2RST_RSEL_T2INPPS, T2HLT_MODE_FR_SOFT_GATE, 
                        T2HLT_PSYNC_OFF, T2HLT_CKPOL_RISING, T2HLT_CKSYNC_ON,
                        true, true, false, false );
    // Initialize PWM 5 Module
    PWM_5_Initialize ( CCPTMRS1_P5TSEL_TMR2, true, true );
    PWM_6_Initialize ( CCPTMRS1_P6TSEL_TMR2, true, true );
    PWM_8_Initialize ( CCPTMRS1_P8TSEL_TMR2, true, true );
    
    // Temporary Variables
    int16_t counter_R   = 0;
    int16_t counter_G   = 341;
    int16_t counter_B   = 682;
    bool    increment_R = true;
    bool    increment_G = true;
    bool    increment_B = true;
    
    // Main Loop
    while(1) { 
        
        // Create a ramp
        if ( increment_R ) {
            // Add to the counter
            counter_R += C_STEP;
            // Change the direction if overflow
            if ( counter_R > PWM_LIM ) {
                // Cap the counter value
                counter_R = PWM_LIM;
                // Start decrementing
                increment_R = false;
            }
        }
        else {
            // Subtract from the counter
            counter_R -= C_STEP;
            // Change the direction if overflow
            if ( counter_R < 0 ) {
                // Cap the counter value
                counter_R = 0;
                // Start incrementing
                increment_R = true;
            }
        }
        // Create a ramp
        if ( increment_G ) {
            // Add to the counter
            counter_G += C_STEP;
            // Change the direction if overflow
            if ( counter_G > PWM_LIM ) {
                // Cap the counter value
                counter_G = PWM_LIM;
                // Start decrementing
                increment_G = false;
            }
        }
        else {
            // Subtract from the counter
            counter_G -= C_STEP;
            // Change the direction if overflow
            if ( counter_G < 0 ) {
                // Cap the counter value
                counter_G = 0;
                // Start incrementing
                increment_G = true;
            }
        }
        // Create a ramp
        if ( increment_B ) {
            // Add to the counter
            counter_B += C_STEP;
            // Change the direction if overflow
            if ( counter_B > PWM_LIM ) {
                // Cap the counter value
                counter_B = PWM_LIM;
                // Start decrementing
                increment_B = false;
            }
        }
        else {
            // Subtract from the counter
            counter_B -= C_STEP;
            // Change the direction if overflow
            if ( counter_B < 0 ) {
                // Cap the counter value
                counter_B = 0;
                // Start incrementing
                increment_B = true;
            }
        }
        
        // Load the values to the PWM Module
        PWM_5_Set_Output_No_Cap ( counter_R );
        PWM_6_Set_Output_No_Cap ( counter_B );
        PWM_8_Set_Output_No_Cap ( counter_G );
        // Delay for effect
        __delay_ms ( 10 ); 
    }

}

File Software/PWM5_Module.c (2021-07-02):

/* 
 * File:                PWM5_Module.c
 * Author:              Provatos Eleftherios
 * Comments:            For use with PIC18F26K83 in OpenServoCAN project
 * Revision history:    V1.00
 */

/* ************************************************************************** */
/* ************************************************************************** */
/* Section: Included Files                                                    */
/* ************************************************************************** */
/* ************************************************************************** */

#include "PWM5_Module.h"
#include "Timer_2.h"
#include "Timer_4.h"
#include "Timer_6.h"

/* ************************************************************************** */
/* ************************************************************************** */
/* Section: File Scope or Global Data                                         */
/* ************************************************************************** */
/* ************************************************************************** */

static uint16_t u16_pwm_val_int = 0;

/* ************************************************************************** */
/* ************************************************************************** */
/* Section: Local Functions                                                   */
/* ************************************************************************** */
/* ************************************************************************** */

// Sets the Timer Source for the PWM 5 Module
static int8_t PWM_5_Set_Timer_Source ( uint8_t timer ) {
    // Check the input if it is in range 0x01 - 0x03
    if ( !( CCPTMRS1_P5TSEL_MASK & timer ) ) {
        // Exit with Error
        return -1;
    }
    // Set the register without changing other bits
    CCPTMRS1 = ( CCPTMRS1 & ~CCPTMRS1_P5TSEL_MASK ) | timer;
    // Return to the point of call with success
    return 1;
}

/* ************************************************************************** */
/* ************************************************************************** */
// Section: Interface Functions                                               */
/* ************************************************************************** */
/* ************************************************************************** */

// Sets the Enable / Disable of the PWM 5 Module
void PWM_5_Set_Enable ( bool en ) {
    // Sets the enable bit according to the input
    if ( en ) {
        // Activate the module
        PWM5CONbits.EN = 1;
    }
    else {
        // Deactivate the module
        PWM5CONbits.EN = 0;
    }
    // Return to the point of call
    return;
}

// Get the Enable / Disable Status of PWM 5 Module
bool PWM_5_Get_Enable ( void ) {
    // Returns the enable bit of the configuration register
    return PWM5CONbits.EN;
}

// Sets the Polarity bit of the PWM 5 Module
void PWM_5_Set_Polarity ( bool inv ) {
    // Sets the polarity of the output
    if ( inv ) {
        // Set to inverted polarity
        PWM5CONbits.POL = 1;
    }
    else {
        // Sets to non - inverted polarity
        PWM5CONbits.POL = 0;
    }
    // Return to the point of call
    return;
}

// Inverts the polarity of the output of PWM 5 Module
void PWM_5_Invert_Polarity ( void ) {
    // Inverts the polarity based on previous state
    if ( PWM5CONbits.POL ) {
        // Since bit is set, reset
        PWM5CONbits.POL = 0;
    }
    else {
        // Since bit is reset, set
        PWM5CONbits.POL = 1;
    }
    // Return to the point of call
    return;
}

// Get the Current Polarity of the output of PWM 5 Module
bool PWM_5_Get_Polarity ( void ) {
    // Returns the polarity bit of the configuration register
    return PWM5CONbits.POL;
}

// Returns the Timer Source of PWM 5 Module
uint8_t PWM_5_Get_Timer_Source ( void ) {
    // Return the Timer settings of PWM 5 Module
    return ( CCPTMRS1 & CCPTMRS1_P5TSEL_MASK );
}

// Set the output with basic check
int8_t PWM_5_Set_Output_No_Cap ( uint16_t pwm_val ) {
    // Check if the value is in range
    if ( pwm_val > 0x3FF ) {
        // Exit with error
        return -1;
    }
    // Check to see if the Value is the old one
    if ( u16_pwm_val_int == pwm_val ) {
        // Exit with no action
        return 0;
    }
    // Update the new value
    u16_pwm_val_int = pwm_val;
    // Load the Timer registers
    PWM5DCH = ( uint8_t ) ( ( pwm_val >> 2 ) & 0xFF );
    PWM5DCL = ( uint8_t ) ( ( pwm_val & 0x03 ) << 0x06 );
    // Exit to program with success
    return 1;
}

// Set the output with Timer Period check check
int8_t PWM_5_Set_Output_Capped ( uint16_t pwm_val ) {
    // Check if the value is in range
    if ( pwm_val > 0x3FF ) {
        // Exit with error
        return -1;
    }
    // Check to see if the Value is the old one
    if ( u16_pwm_val_int == pwm_val ) {
        // Exit with no action
        return 0;
    }
    // Cap the Value according to the corresponding Timer period value
    switch ( PWM_5_Get_Timer_Source ( ) ) {
        // Case TMR2 is used, cap based on TMR2PR
        case CCPTMRS1_P5TSEL_TMR2 : {
            // Temporary variable
            uint16_t temp = ( uint16_t ) Timer_2_Period_Get ( ) << 2;
            // Check for the value
            if ( pwm_val > temp ) {
                // Cap the PWM Value
                pwm_val = temp;
            }
            // Exit switch
            break;
        }
        // Case TMR2 is used, cap based on TMR2PR
        case CCPTMRS1_P5TSEL_TMR4 : {
            // Temporary variable
            uint16_t temp = ( ( uint16_t ) Timer_4_Period_Get ( ) ) << 2;
            // Check for the value
            if ( pwm_val > temp ) {
                // Cap the PWM Value
                pwm_val = temp;
            }
            // Exit switch
            break;
        }
        // Case TMR2 is used, cap based on TMR2PR
        case CCPTMRS1_P5TSEL_TMR6 : {
            // Temporary variable
            uint16_t temp = ( ( uint16_t ) Timer_6_Period_Get ( ) ) << 2;
            // Check for the value
            if ( pwm_val > temp ) {
                // Cap the PWM Value
                pwm_val = temp;
            }
            // Exit switch
            break;
        }
        // Case something is wrong
        default : {
            // Exit with an error - Timer source error
            return -1;
        }
    }
    // Update the new value
    u16_pwm_val_int = pwm_val;
    // Load the Timer registers
    PWM5DCH = ( uint8_t ) ( ( pwm_val >> 2 ) & 0xFF );
    PWM5DCL = ( uint8_t ) ( ( pwm_val & 0x03 ) << 0x06 );
    // Exit to program with success
    return 1;
}
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

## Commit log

2020-03-28 commit message
    [TRN_Open_Servo.brd, TRN_Open_Servo.sch]
2020-06-15 #1 Timer_Support_Library
    [configuration_pins.h]
2020-08-03 #1 Some Suport for MCU peripherals added
    - Added support for PWM related timers and comperators.
    - Next update should handle the Interrupts
2020-08-07 #1 Added Interrupt Service Routines (Empty) - Added Initial Supprot for CWG Modules
2020-12-01 #2
    File Preparing Step 1
    [TRN_Open_Servo.brd, TRN_Open_Servo.sch]
2021-01-04 #2 Hardware Ver.2 Upload
    All three boards of Version 2 are uploaded:
    - Power Delivery Board ver 1.01
    - Microcontroller Board ver 1.01
    - Magnetic Encoder Board ver 1.01
    I have to see if I need to utilize enable pin of the 3V3 Regulator of the magnetic board to lower power consumption on idle, but for now that is good enough!
    I also have to see if I can fit another board in there, cause then we are going for accelerometer and gyro! And that could be the end game for "edge controlling (ahem computing).
    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
    [OpenServoCAN_Encoder_Board_V_1_0_1.brd, OpenServoCAN_Encoder_Board_V_1_0_1.sch, OpenServoCAN_Microcontroller_Board_V_1_0_1.brd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]
2021-06-22 Note to PCB changes
    Layout of the Power Board PCB has to be changed.
2021-07-02 PWM, Timers and PPS
    - Fixed Timer 2 / 4 / 6 libraries. Fixed logic errors in the libraries.
    - Added the Libraries for PWM 5 / 6 / 7 / 8.
    - Fixed / Configured Correctly the PPS for outputs.
    NOTE: PPS is different for inputs and outputs. A pin is configured with a module output. A module input is configured with a pin.
    Demo: RGB LED Demo cycling colors.
    [PWM5_Module.c, PWM6_Module.c, PWM7_Module.c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]

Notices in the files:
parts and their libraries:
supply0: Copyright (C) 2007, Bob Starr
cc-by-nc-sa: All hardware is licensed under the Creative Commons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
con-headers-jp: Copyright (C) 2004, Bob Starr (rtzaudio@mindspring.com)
